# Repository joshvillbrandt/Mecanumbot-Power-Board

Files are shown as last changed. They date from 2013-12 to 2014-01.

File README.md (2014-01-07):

Mecanumbot Power Board
======================

The power board for the Mecanumbot robot.

## Features

* automatically selects between two batteries and the wall
* chooses the wall if available, otherwise drains the batteries one at a time
* provides power voltage and current measuring
* communicates to the primary vehicle Arduino over I2C
* provides regulated 5V power for the robot LEDs
* provides pins for an external switch

See more at http://javconcepts.com/2013/01/06/mecanumbot-power-board/.

## Todo List

* add battery charging
 * the [MAX164*](http://www.maximintegrated.com/datasheet/index.mvp/id/1751) can [allegedly](http://letsmakerobots.com/node/28374?page=1) charge up to a six cell lipo; i'm not sure if that includes balancing the cell or not too
* add fusing
* keep the board / robot powered during microcontroller restart by using flip-flops (useful for loading new code from the robot itself)
 * this could enable comm directly with ROS via USB instead of through I2C through the other Arduino!

## Screenshot

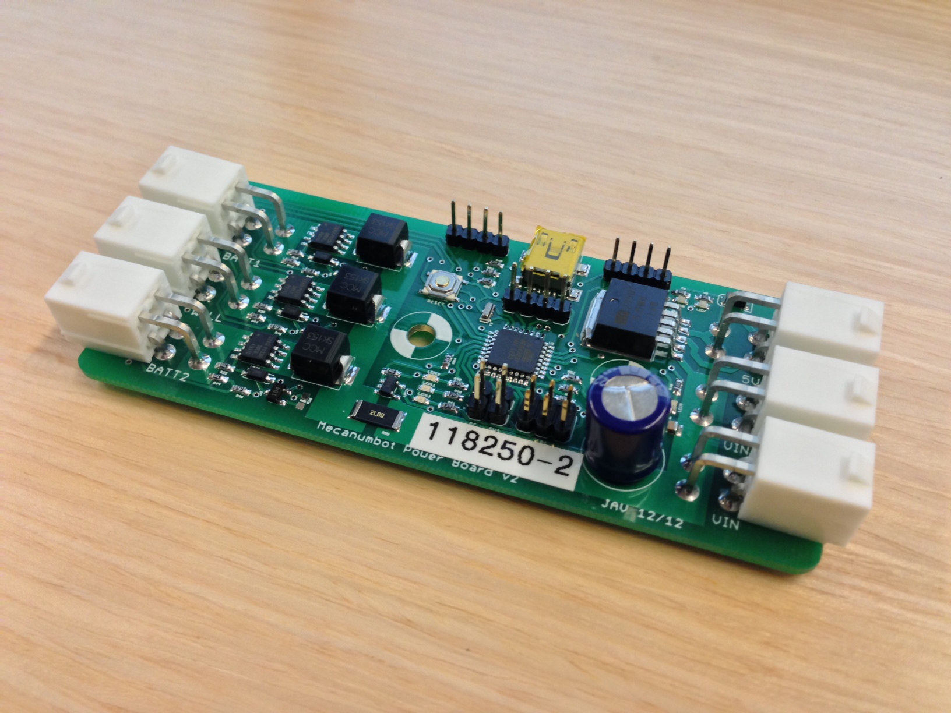
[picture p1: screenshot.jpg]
Assembled PCB Screenshot


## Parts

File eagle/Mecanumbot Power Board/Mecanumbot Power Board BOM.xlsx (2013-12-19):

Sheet: v1 BOM
Part | Value | Package | Description | Digi-Key PN | Cost
C2 | 1uF | 0603-CAP | Capacitor | 445-3452-1-ND | $0.03
C3 | 1uF | 0603-CAP | Capacitor | 445-3452-1-ND | $0.03
C4 | 0.1uF | 0603-CAP | Capacitor | 445-1316-1-ND | $0.01
C5 | 330uF | EIA3528 | footprint is wrong, but should work | P15095CT-ND | $0.92
C6 | 1uF | 0603-CAP | Capacitor | 445-3452-1-ND | $0.03
C7 | 0.1uF | 0603-CAP | Capacitor | 445-1316-1-ND | $0.01
C8 | 0.1uF | 0603-CAP | Capacitor | 445-1316-1-ND | $0.01
C10 | 0.1uF | 0603-CAP | Capacitor | 445-1316-1-ND | $0.01
C12 | 1uF | 0603-CAP | Capacitor | 445-3452-1-ND | $0.03
C13 | 1uF | 0603-CAP | Capacitor | 445-3452-1-ND | $0.03
C14 | 1uF | 0603-CAP | Capacitor | 445-3452-1-ND | $0.03
C15 | 0.1uF | 0603-CAP | Capacitor | 445-1316-1-ND | $0.01
C16 | 330uF | EIA3528 | footprint is wrong, but should work | P15095CT-ND | $0.92
C17 | 1uF | 0603-CAP | Capacitor | 445-3452-1-ND | $0.03
C18 | 68uF | EIA3216 | Capacitor Polarized | 493-6545-1-ND | $0.80
C19 | 220uF | CPOL-RADIAL-1000UF-25V | Capacitor Polarized | P5183-ND | $0.44
C21 | 0.1uF | 1206 | Capacitor | 399-1249-1-ND | $0.07
C22 | 0.1uF | 0603-CAP | Capacitor | 445-1316-1-ND | $0.01
C35 | 100uF | EIA3216 | Capacitor Polarized | 493-6545-1-ND | $0.80
J1 | AVR_SPI_PRG_6PTH | 2X3 | AVR ISP 6 Pin | 3M9459-ND | $0.42
JP1 | S2 | 1X02 | Header 2 | WM6436-ND | $0.90
JP6 | PWR LED | 1X02 | Header 2 | WM6436-ND | $0.90
JP7 | I2C | 1X04 | Header 4 | WM6436-ND | $0.90
LED1 | Red | LED-0603 | LEDs | 475-2512-1-ND | $0.08
LED2 | Yellow | LED-0603 | LEDs | 475-2558-1-ND | $0.08
LED3 | Green | LED-0603 | LEDs | 475-1409-1-ND | $0.07
LED4 | RED | LED5MM | LEDs | 1080-1120-ND | $0.33
LED5 | RED | LED5MM | LEDs | 1080-1120-ND | $0.33
LED6 | RED | LED5MM | LEDs | 1080-1120-ND | $0.33
Q1 |  | SOT23 | Transistor NPN | ZXTN07045EFFCT-ND | $0.59
Q2 |  | SOT23 | Transistor NPN | ZXTN07045EFFCT-ND | $0.59
Q3 |  | SOT23 | Transistor NPN | ZXTN07045EFFCT-ND | $0.59
R1 | 330 | 0603-RES | Resistor | 311-330GRCT-ND | $0.0048
R2 | 330 | 0603-RES | Resistor | 311-330GRCT-ND | $0.0048
R3 | 10K | 0603-RES | Resistor | 311-10KGRCT-ND | $0.0048
R4 | 7.5K | 0603-RES | Resistor | 311-7.5KGRCT-ND | $0.01
R5 | 7.5K | 0603-RES | Resistor | 311-7.5KGRCT-ND | $0.01
R6 | 200K | 0603-RES | Resistor | 311-200KGRCT-ND | $0.01
R7 | 24K | 0603-RES | Resistor | 311-24KGRCT-ND | $0.01
R8 | 1K | 0603-RES | Resistor | 311-1.0KGRCT-ND | $0.01
R9 | 200K | 0603-RES | Resistor | 311-200KGRCT-ND | $0.01
R10 | 24K | 0603-RES | Resistor | 311-24KGRCT-ND | $0.01
R11 | 1K | 0603-RES | Resistor | 311-1.0KGRCT-ND | $0.01
R12 | 10K | 0603-RES | Resistor | 311-10KGRCT-ND | $0.0048
R13 | 10K | 0603-RES | Resistor | 311-10KGRCT-ND | $0.0048
R14 | 10K | 0603-RES | Resistor | 311-10KGRCT-ND | $0.0048
R15 | 10K | 0603-RES | Resistor | 311-10KGRCT-ND | $0.0048
R16 | 10K | 0603-RES | Resistor | 311-10KGRCT-ND | $0.0048
R17 | 10K | 0603-RES | Resistor | 311-10KGRCT-ND | $0.0048
R18 | 330 | 0603-RES | Resistor | 311-330GRCT-ND | $0.0048
R19 | 330 | 0603-RES | Resistor | 311-330GRCT-ND | $0.0048
R20 | 330 | 0603-RES | Resistor | 311-330GRCT-ND | $0.0048
R21 | 330 | 0603-RES | Resistor | 311-330GRCT-ND | $0.0048
R22 | 10K | 0603-RES | Resistor | 311-10KGRCT-ND | $0.0048
R23 | 10K | 0603-RES | Resistor | 311-10KGRCT-ND | $0.0048
R24 | 10K | 0603-RES | Resistor | 311-10KGRCT-ND | $0.0048
R25 | 10K | 0603-RES | Resistor | 311-10KGRCT-ND | $0.0048
R26 | 3.3K | 0603-RES | Resistor | 311-3.3KGRCT-ND | $0.0048
R27 | 3.3K | 0603-RES | Resistor | 311-3.3KGRCT-ND | $0.0048
R28 | 3.3K | 0603-RES | Resistor | 311-3.3KGRCT-ND | $0.0048
R29 | 3.3K | 0603-RES | Resistor | 311-3.3KGRCT-ND | $0.0048
R30 | 330 | 0603-RES | Resistor | 311-330GRCT-ND | $0.0048
R31 | 82.5K 1% | 0603-RES | Resistor | 311-82.5KHRCT-ND | $0.01
R32 | 0.002 1% 2W | R2512 | Resistor | RHM.002AUCT-ND | $0.85
R33 | 3.3K | 0603-RES | Resistor | 311-3.3KGRCT-ND | $0.0048
R34 | 10K | 0603-RES | Resistor | 311-10KGRCT-ND | $0.0048
R35 | 10k | 0603-RES | Resistor | 311-10KGRCT-ND | $0.0048
R36 | 10k | 0603-RES | Resistor | 311-10KGRCT-ND | $0.0048
R37 | 10k | 0603-RES | Resistor | 311-10KGRCT-ND | $0.0048
S1 | reset | TACTILE_SWITCH_SMD |  | CKN9104CT-ND | $0.61
U$1 | IR3477 | IR3477 |  | IR3477MTR1PBFCT-ND | $6.35
U$2 | 1uH | CDRH125 | Inductors | 308-1334-1-ND | $1.35
U$3 | IR3477 | IR3477 |  | IR3477MTR1PBFCT-ND | $6.35
U$4 | 1uH | CDRH125 | Inductors | 308-1334-1-ND | $1.35
U$5 | DIODE_SCHOTTKY | DO214AB |  | SK153-TPCT-ND | $1.19
U$6 | MOSFET-PCHANNEL-SOIC8SOIC8 | SO08 |  | IRF9310TRPBFCT-ND | $1.36
U$7 | MOSFET-PCHANNEL-SOIC8SOIC8 | SO08 |  | IRF9310TRPBFCT-ND | $1.36
U$8 | DIODE_SCHOTTKY | DO214AB |  | SK153-TPCT-ND | $1.19
U$9 | TERMINAL-4MINIFIT-JR | MINIFITJR-RGT-4 |  | WM21352-ND | $0.84
U$10 | MOSFET-PCHANNEL-SOIC8SOIC8 | SO08 |  | IRF9310TRPBFCT-ND | $1.36
U$11 | DIODE_SCHOTTKY | DO214AB |  | SK153-TPCT-ND | $1.19
U$12 | TERMINAL-4MINIFIT-JR | MINIFITJR-RGT-4 |  | WM21352-ND | $0.84
U$13 | TERMINAL-4MINIFIT-JR | MINIFITJR-RGT-4 |  | WM21352-ND | $0.84
U$14 | TERMINAL-4MINIFIT-JR | MINIFITJR-RGT-4 |  | WM21352-ND | $0.84
U$15 | TERMINAL-4MINIFIT-JR | MINIFITJR-RGT-4 |  | WM21352-ND | $0.84
U$16 | TERMINAL-4MINIFIT-JR | MINIFITJR-RGT-4 |  | WM21352-ND | $0.84
U$17 | TERMINAL-4MINIFIT-JR | MINIFITJR-RGT-4 |  | WM21352-ND | $0.84
U$18 | TERMINAL-4MINIFIT-JR | MINIFITJR-RGT-4 |  | WM21352-ND | $0.84
U$19 | VREG-MIC29501-5V | TO263-5 |  | 576-2240-ND | $5.60
U$20 | INA139/169SOT23-5 | SOT23-5 | TI High-Side Measurement: CURRENT SHUNT MONITOR | INA139NA/250CT-ND | $2.15
U$21 | SUPERCAPS-LEAD | AVX-SUPERCAP-S-LEAD | CAP SUPER 6.8MF 15V BZ05 SMD | 478-6277-ND | $16.36
U$22 | HMC6352 | LCC24 | HMC6352 | 342-1041-1-ND | $26.00
U1 | FT232RL-BASICSSOP | SSOP28DB | USB UART | 768-1007-1-ND | $4.50
U2 | ATMEGA168 | TQFP32-08 |  | ATMEGA328P-AU-ND | $3.05
X1 | USBSMD | USB-MINIB | USB Connectors | ED2992CT-ND | $0.68
Y1 | RESONATORSMD | RESONATOR-SMD | Resonator | 490-1198-1-ND | $0.95
Total |  |  |  |  | $101.10
 | fuse holder | http://www.digikey.com/product-detail/en/01530008Z/F065-ND/183334
 | fuse | http://www.digikey.com/product-detail/en/0297015.WXNV/F992-ND/146594
 |  | http://www.digikey.com/product-detail/en/MB2181SS1W01-CA/360-2178-ND/1014874

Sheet: v2 BOM
Qty | Parts | Digi-Key PN | Value | Device | Package | Description | Cost | Sub-total
12 | R3, R6, R12, R13, R14, R15, R16, R17, R23, R24, R25, R34, R37 | 311-10.0KHRCT-ND | 10K | RESISTOR0603-RES | 0603-RES | Resistor | $0.10 | $1.20
8 | R1, R2, R4, R18, R19, R20, R21, R30 | 311-330GRCT-ND | 330 | RESISTOR0603-RES | 0603-RES | Resistor | $0.0048 | $0.04
6 | U$12, U$13, U$14, U$16, U$17, U$18 | WM21352-ND | TERMINAL-4MINIFIT-JR | TERMINAL-4MINIFIT-JR | MINIFITJR-RGT-4 |  | $0.84 | $5.04
5 | R7, R27, R28, R29, R33 | 311-3.30KHRCT-ND | 3.3K | RESISTOR0603-RES | 0603-RES | Resistor | $0.10 | $0.50
3 | Q1, Q2, Q3 | ZXTN07045EFFCT-ND |  | TRANSISTOR_NPNSOT23 | SOT23 | Transistor NPN | $0.59 | $1.77
3 | C7, C8, C10 | 445-1316-1-ND | .1uF | CAP0603-CAP | 0603-CAP | Capacitor | $0.01 | $0.03
3 | U$2, U$3, U$4 | BZT52C33-FDICT-ND | BZT52C33-FDICT-ND | BZT52C33-FDICT-ND | SOD-123 | 33V Zener Diode, 500mW | $0.21 | $0.63
3 | U$5, U$8, U$11 | SK153-TPCT-ND | DIODE_SCHOTTKY | DIODE_SCHOTTKY | DO214AB |  | $1.19 | $3.57
3 | U$6, U$7, U$10 | IRF9310TRPBFCT-ND | MOSFET-PCHANNEL-SOIC8SOIC8 | MOSFET-PCHANNEL-SOIC8SOIC8 | SO08 |  | $1.36 | $4.08
3 | LED4, LED5, LED6 | 475-2816-1-ND | Blue | LED0603 | LED-0603 | LEDs | $0.17 | $0.52
2 | JP1, PC-CTRL | WM6436-ND | S2 | M02PTH | 1X02 | Header 2 | $0.90 | $1.80
2 | LED2, LED3 | 475-2558-1-ND | Yellow | LED0603 | LED-0603 | LEDs | $0.08 | $0.16
1 | R32 | RHM.002AUCT-ND | 0.002 1% 2W | RESISTOR2512 | R2512 | Resistor | $0.85 | $0.85
1 | C21 | 399-1249-1-ND | 0.1uF | CAP1206 | 1206 | Capacitor | $0.07 | $0.07
1 | C35 | 493-6545-1-ND | 100uF | CAP_POL1206 | EIA3216 | Capacitor Polarized | $0.80 | $0.80
1 | C19 | P5183-ND | 220uF | CAP_POLPTH4 | CPOL-RADIAL-1000UF-25V | Capacitor Polarized | $0.44 | $0.44
1 | R31 | 311-82.5KHRCT-ND | 82.5K 1% | RESISTOR0603-RES | 0603-RES | Resistor | $0.01 | $0.01
1 | U2 | ATMEGA328P-AU-ND | ATMEGA168 | ATMEGA168 | TQFP32-08 |  | $3.05 | $3.05
1 | J1 | 3M9459-ND | AVR_SPI_PRG_6PTH | AVR_SPI_PRG_6PTH | 2X3 | AVR ISP 6 Pin | $0.42 | $0.42
1 | U$1 | CLA230TR-ND | CLA230TR-NDSMD | CLA230TR-NDSMD | 4-SOP | Digi-Key part: CLA230TR-ND | $0.63 | $0.63
1 | U1 | 768-1007-1-ND | FT232RL-BASICSSOP | FT232RL-BASICSSOP | SSOP28DB | USB UART | $4.50 | $4.50
1 | LED1 | 475-2512-1-ND | RED | LED0603 | LED-0603 | LEDs | $0.08 | $0.08
1 | JP2, JP3, JP7 | WM6436-ND | USB, PWR-CTRL, I2C | M04PTH | 1X04 | Header 4 | $0.90 | $0.90
1 | U$20 | INA139NA/250CT-ND | INA139/169SOT23-5 | INA139/169SOT23-5 | SOT23-5 | TI High-Side Measurement: CURRENT SHUNT MONITOR | $2.15 | $2.15
1 | Y1 | 490-1198-1-ND | RESONATORSMD | RESONATORSMD | RESONATOR-SMD | Resonator | $0.95 | $0.95
1 | X1 | ED2992CT-ND | USBSMD | USBSMD | USB-MINIB | USB Connectors | $0.68 | $0.68
1 | U$19 | 576-2240-ND | VREG-MIC29501-5V | VREG-MIC29501-5V | TO263-5 |  | $5.60 | $5.60
1 | S1 | CKN9104CT-ND | reset | SWITCH-MOMENTARY-2SMD | TACTILE_SWITCH_SMD |  | $0.61 | $0.61
Total |  |  |  |  |  |  |  | $41.08

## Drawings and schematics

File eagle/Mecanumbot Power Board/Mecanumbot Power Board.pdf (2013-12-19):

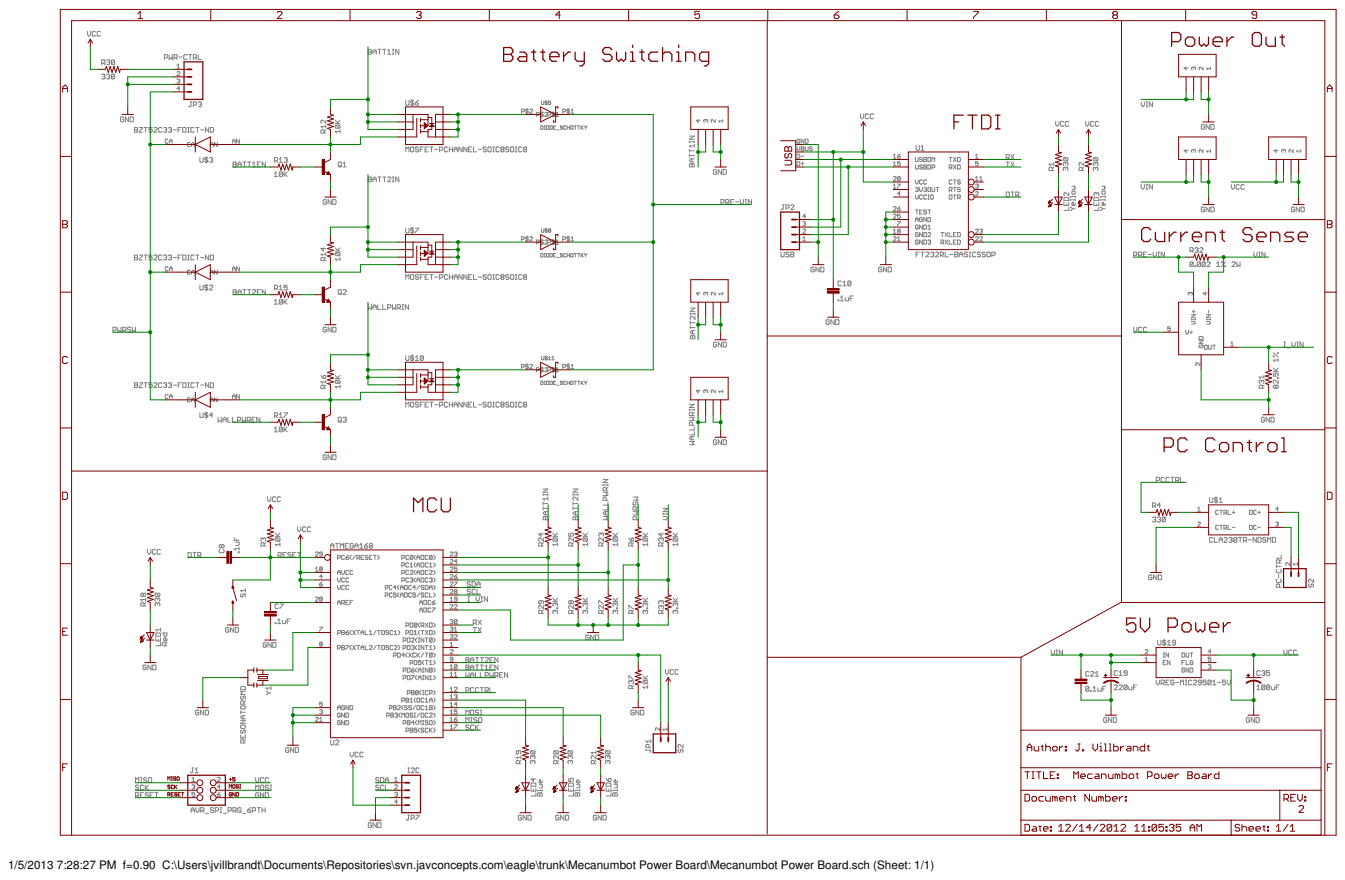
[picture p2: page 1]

1/5/2013 7:28:27 PM f=0.90 C:\Users\jvillbrandt\Documents\Repositories\svn.javconcepts.com\eagle\trunk\Mecanumbot Power Board\Mecanumbot Power Board.sch (Sheet: 1/1)

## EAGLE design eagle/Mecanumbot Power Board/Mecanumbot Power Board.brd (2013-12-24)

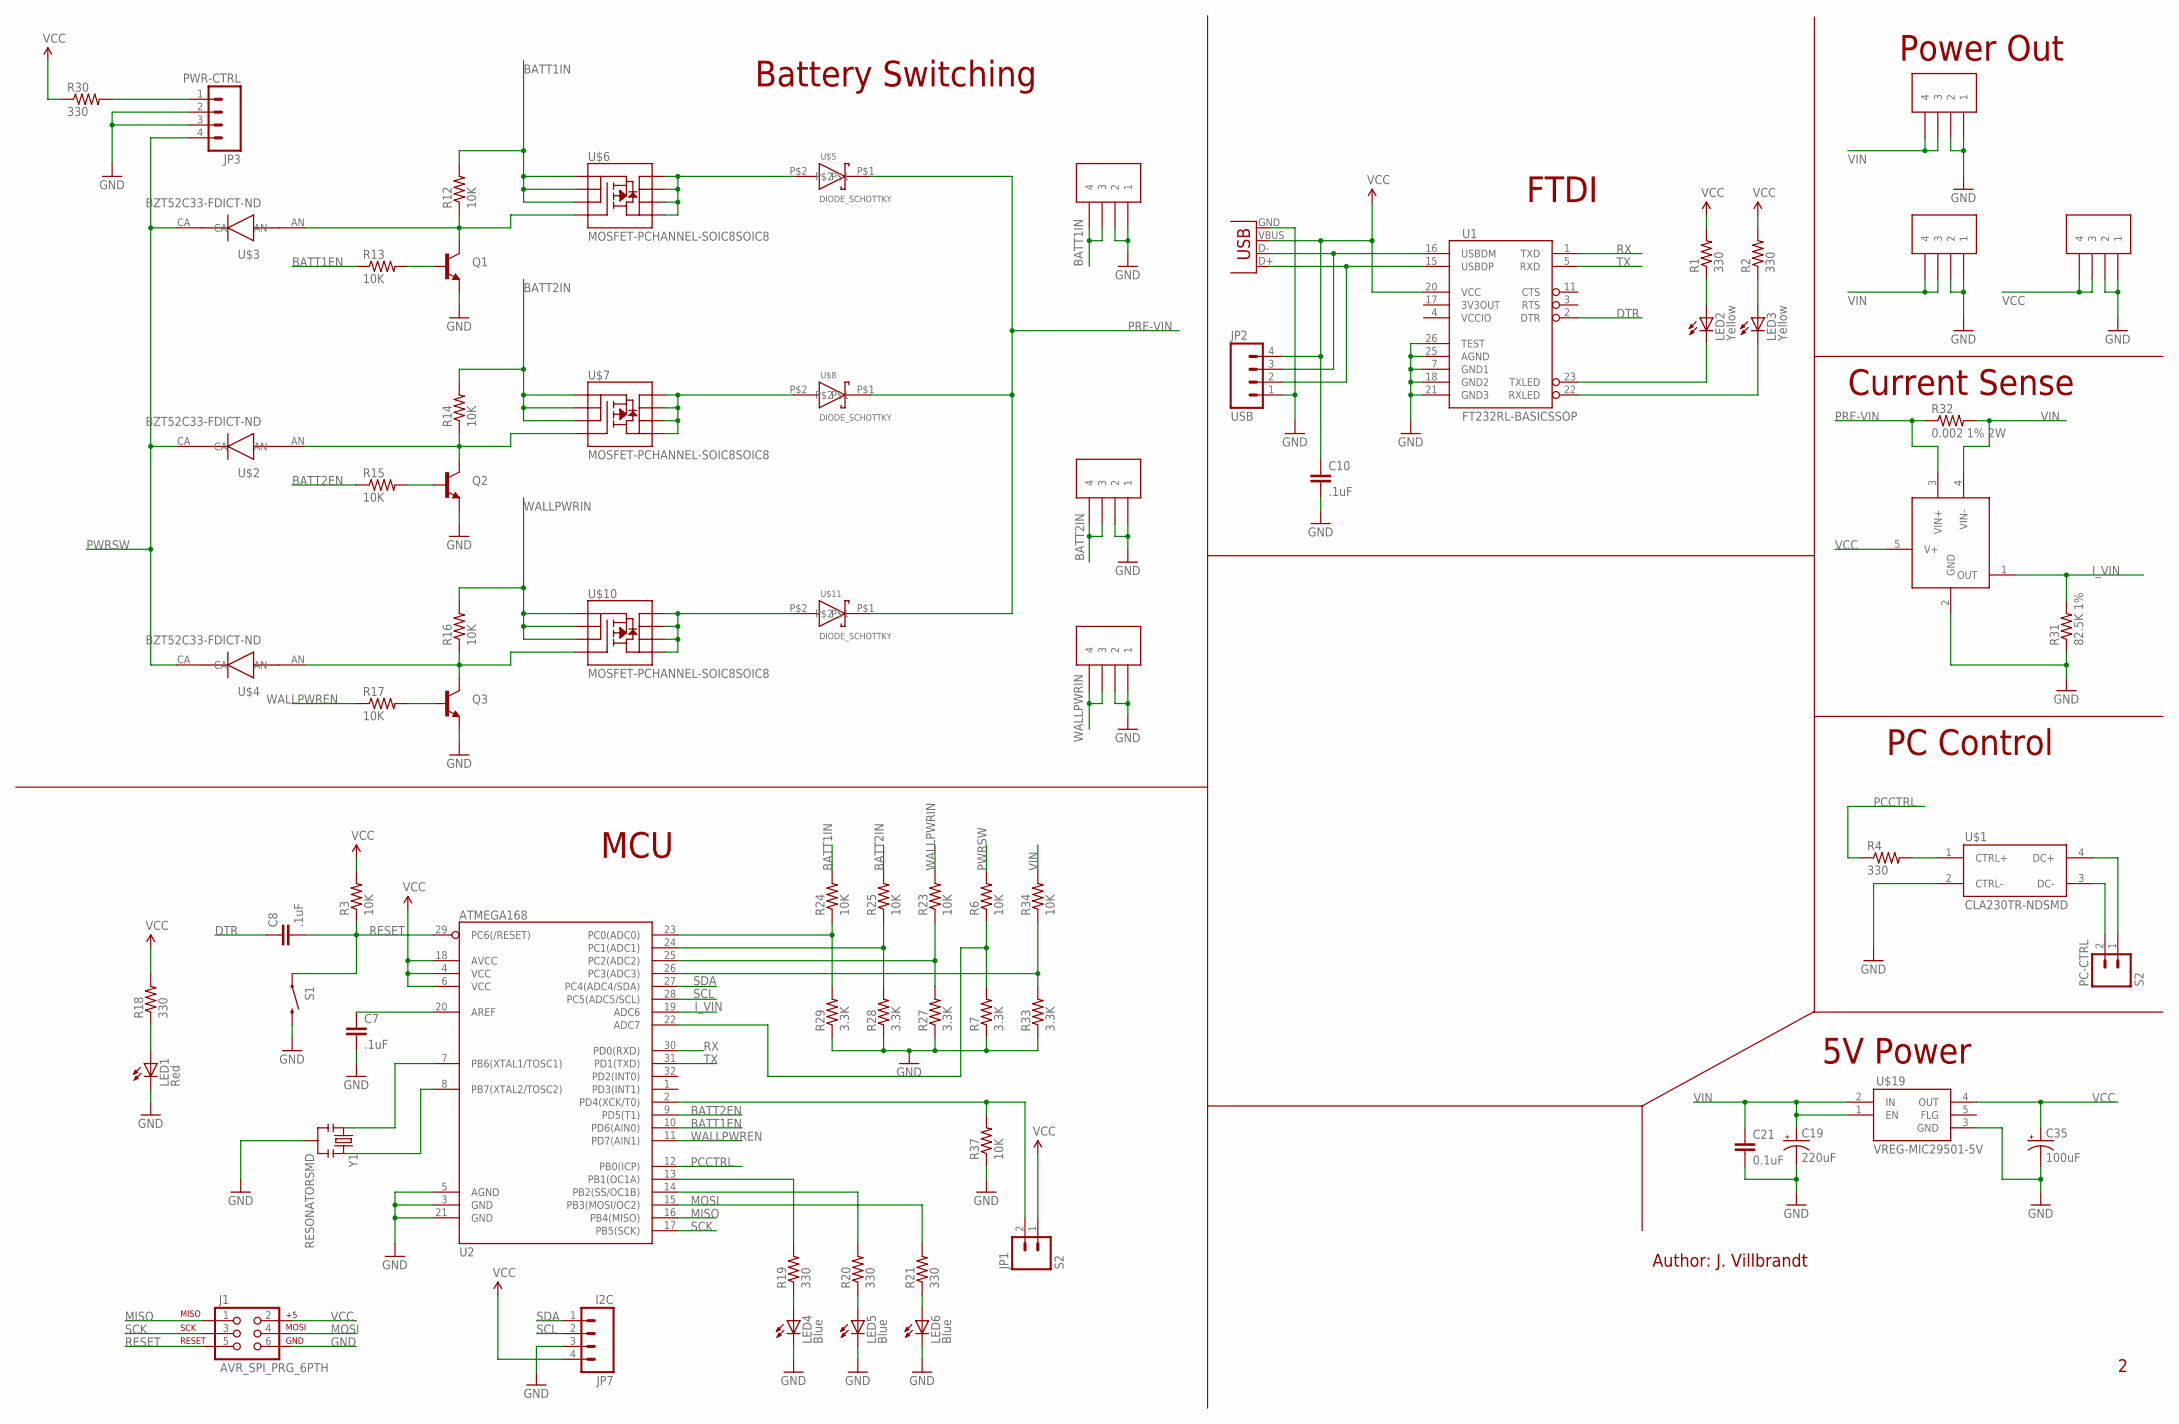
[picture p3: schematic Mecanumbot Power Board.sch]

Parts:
C7, C8, C10: .1uF; 0603-CAP
C19: 220uF; CPOL-RADIAL-1000UF-25V
C21: 0.1uF; 1206
C35: 100uF; EIA3216
J1: AVR_SPI_PRG_6PTH; 2X3
JP1: S2; 1X02
JP2: USB; 1X04
JP3: PWR-CTRL; 1X04
JP7: I2C; 1X04
LED1: Red; LED-0603
LED2, LED3: Yellow; LED-0603
LED4, LED5, LED6: Blue; LED-0603
PC-CTRL: S2; 1X02
Q1, Q2, Q3: TRANSISTOR_NPNSOT23; SOT23
R1, R2, R4, R18, R19, R20, R21, R30: 330; 0603-RES
R3, R6, R12, R13, R14, R15, R16, R17, R23, R24, R25, R34, R37: 10K; 0603-RES
R7, R27, R28, R29, R33: 3.3K; 0603-RES
R31: 82.5K 1%; 0603-RES
R32: 0.002 1% 2W; R2512
S1: reset; TACTILE_SWITCH_SMD
U1: FT232RL-BASICSSOP; SSOP28DB
U2: ATMEGA168; TQFP32-08
U$1: CLA230TR-NDSMD; 4-SOP
U$2, U$3, U$4: BZT52C33-FDICT-ND; SOD-123
U$5, U$8, U$11: DIODE_SCHOTTKY; DO214AB
U$6, U$7, U$10: MOSFET-PCHANNEL-SOIC8SOIC8; SO08
U$12, U$13, U$14, U$16, U$17, U$18: TERMINAL-4MINIFIT-JR; MINIFITJR-RGT-4
U$19: VREG-MIC29501-5V; TO263-5
U$20: INA139/169SOT23-5; SOT23-5
X1: USBSMD; USB-MINIB
Y1: RESONATORSMD; RESONATOR-SMD

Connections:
BATT1EN: R13.1, U2.10 (PD6(AIN0))
BATT1IN: R12.2, R24.2, U$6.1 (S), U$6.2 (S), U$6.3 (S), U$12.3, U$12.4
BATT1PREDIODE: U$5.P$2, U$6.5 (D), U$6.6 (D), U$6.7 (D), U$6.8 (D)
BATT2EN: R15.1, U2.9 (PD5(T1))
BATT2IN: R14.2, R25.2, U$7.1 (S), U$7.2 (S), U$7.3 (S), U$13.3, U$13.4
BATT2PREDIODE: U$7.5 (D), U$7.6 (D), U$7.7 (D), U$7.8 (D), U$8.P$2
DTR: C8.1, U1.2 (DTR)
GND: C7.2, C10.2, C19.2 (-), C21.2, C35.C (-), J1.6, JP2.1, JP3.2, JP3.3, JP7.3, LED1.C, LED4.C, LED5.C, LED6.C, Q1.2 (E), Q2.2 (E), Q3.2 (E), R7.1, R27.1, R28.1, R29.1, R31.1, R33.1, R37.1, S1.3 (2), U1.7 (GND1), U1.18 (GND2), U1.21 (GND3), U1.25 (AGND), U1.26 (TEST), U2.3 (GND), U2.5 (AGND), U2.21 (GND), U$1.2 (CTRL-), U$12.1, U$12.2, U$13.1, U$13.2, U$14.1, U$14.2, U$16.1, U$16.2, U$17.1, U$17.2, U$18.1, U$18.2, U$19.3 (GND), U$20.2 (GND), X1.GND, Y1.2
I_VIN: R31.2, U2.19 (ADC6), U$20.1 (OUT)
MISO: J1.1, U2.16 (PB4(MISO))
MOSI: J1.4, R21.2, U2.15 (PB3(MOSI/OC2))
unnamed: LED2.A, R1.1
unnamed: LED3.A, R2.1
unnamed: LED2.C, U1.23 (TXLED)
unnamed: LED3.C, U1.22 (RXLED)
unnamed: PC-CTRL.2, U$1.3 (DC-)
unnamed: PC-CTRL.1, U$1.4 (DC+)
unnamed: JP2.3, U1.16 (USBDM), X1.D-
unnamed: JP2.2, U1.15 (USBDP), X1.D+
unnamed: C7.1, U2.20 (AREF)
unnamed: U2.7 (PB6(XTAL1/TOSC1)), Y1.1
unnamed: U2.8 (PB7(XTAL2/TOSC2)), Y1.3
unnamed: R4.2, U$1.1 (CTRL+)
unnamed: JP3.1, R30.2
unnamed: R20.2, U2.14 (PB2(SS/OC1B))
unnamed: R33.2, R34.1, U2.26 (PC3(ADC3))
unnamed: R19.2, U2.13 (PB1(OC1A))
unnamed: JP1.2, R37.2, U2.2 (PD4(XCK/T0))
unnamed: Q1.3 (C), R12.1, U$3.AN, U$6.4 (G)
unnamed: Q1.1 (B), R13.2
unnamed: Q2.3 (C), R14.1, U$2.AN, U$7.4 (G)
unnamed: Q2.1 (B), R15.2
unnamed: LED1.A, R18.1
unnamed: Q3.3 (C), R16.1, U$4.AN, U$10.4 (G)
unnamed: Q3.1 (B), R17.2
unnamed: LED6.A, R21.1
unnamed: LED4.A, R19.1
unnamed: LED5.A, R20.1
unnamed: R23.1, R27.2, U2.25 (PC2(ADC2))
unnamed: R25.1, R28.2, U2.24 (PC1(ADC1))
unnamed: R24.1, R29.2, U2.23 (PC0(ADC0))
unnamed: R6.1, R7.2, U2.22 (ADC7)
PCCTRL: R4.1, U2.12 (PB0(ICP))
PRE-VIN: R32.1, U$5.P$1, U$8.P$1, U$11.P$1, U$20.3 (VIN+)
PWRSW: JP3.4, R6.2, U$2.CA, U$3.CA, U$4.CA
RESET: C8.2, J1.5, R3.1, S1.1, U2.29 (PC6(/RESET))
RX: U1.1 (TXD), U2.30 (PD0(RXD))
SCK: J1.3, U2.17 (PB5(SCK))
SCL: JP7.2, U2.28 (PC5(ADC5/SCL))
SDA: JP7.1, U2.27 (PC4(ADC4/SDA))
TX: U1.5 (RXD), U2.31 (PD1(TXD))
VCC: C10.1, C35.A (+), J1.2, JP1.1, JP2.4, JP7.4, R1.2, R2.2, R3.2, R18.2, R30.1, U1.20 (VCC), U2.4 (VCC), U2.6 (VCC), U2.18 (AVCC), U$18.3, U$18.4, U$19.4 (OUT), U$20.5 (V+), X1.VBUS
VCCIO: U1.4 (VCCIO)
VIN: C19.1 (+), C21.1, R32.2, R34.2, U$16.3, U$16.4, U$17.3, U$17.4, U$19.1 (EN), U$19.2 (IN), U$20.4 (VIN-)
WALLPWREN: R17.1, U2.11 (PD7(AIN1))
WALLPWRIN: R16.2, R23.2, U$10.1 (S), U$10.2 (S), U$10.3 (S), U$14.3, U$14.4
WALLPWRPREDIODE: U$10.5 (D), U$10.6 (D), U$10.7 (D), U$10.8 (D), U$11.P$2

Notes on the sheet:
Battery Switching
MCU
FTDI
5V Power
Power Out
Current Sense
Author: J. Villbrandt
PC Control

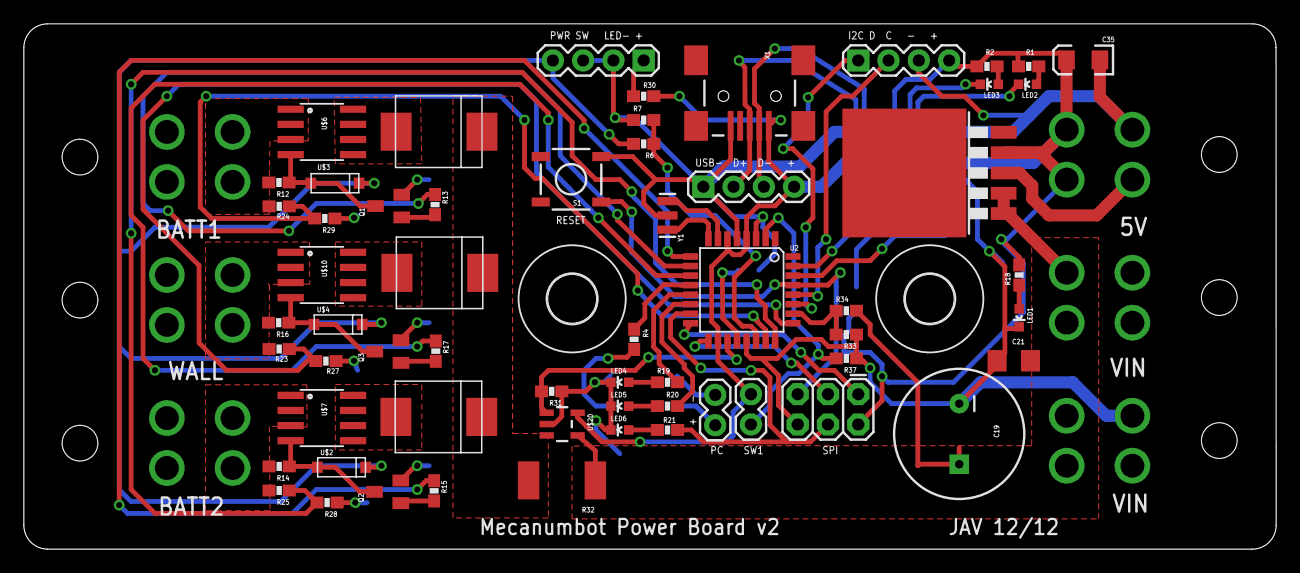
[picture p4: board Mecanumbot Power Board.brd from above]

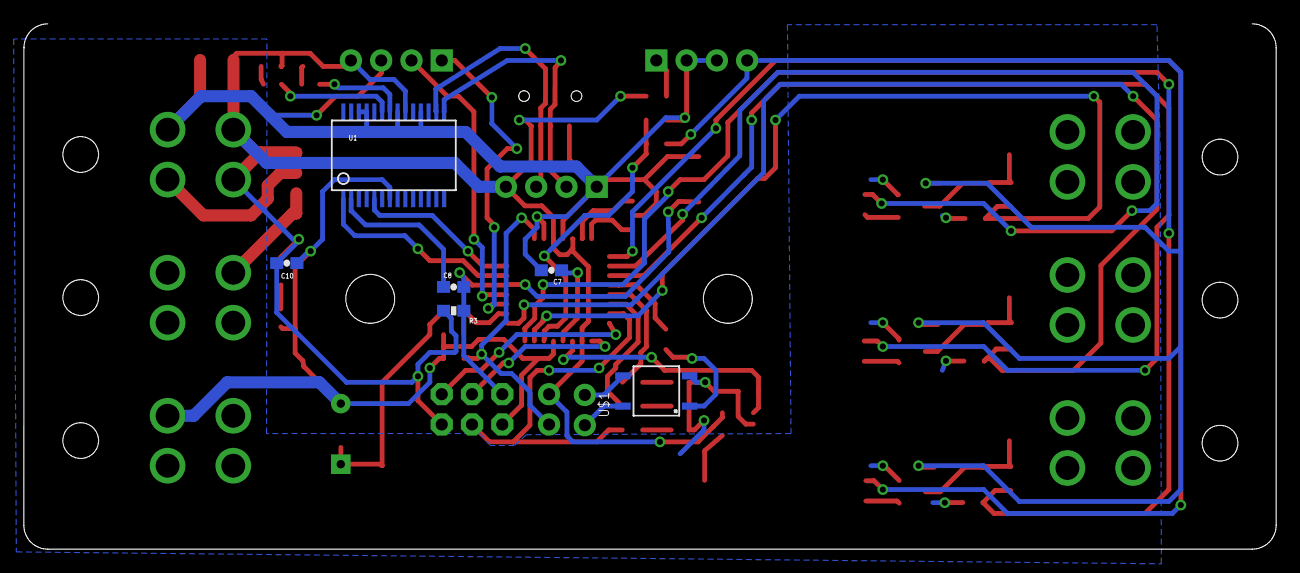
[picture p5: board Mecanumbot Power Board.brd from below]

Board: 2 copper layers, 105.1 x 44.1 mm, 74 parts (6 on the bottom side), 56 nets.

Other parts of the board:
U$24, U$26: 4,1

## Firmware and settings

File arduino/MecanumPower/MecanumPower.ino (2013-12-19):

/*
  MecanumPower.ino - Controls power input for the Mecanumbot.
  Created by Josh Villbrandt (http://javconcepts.com/), 10/12-1/13.
  Released into the public domain.
*/

// Set up I2C
//#include <Wire.h>

#define DEBUG false
#define PC_STARTUP true
#define REF_5V 4.973 // V
#define ADC_COUNTS 1023.0 // counts
#define ADC_V_MULT ((REF_5V / ADC_COUNTS) / 0.24) // counts to V
#define ADC_I_MULT ((REF_5V / ADC_COUNTS) * (1000.0 / (0.002 * 82500))) // counts to A
#define MIN_VOLT 10.5 // V
#define TURN_OFF_DEBOUNCE 1500 // ms
#define LED_RATE 100 // ms
#define LED_DUTY 65 // ms

// Define I/O pins
#define EXT_SW 4
#define EXT_PC 8
byte ledPins[] = {10, 9, 11}; //wall, batt1, batt2
byte fetPins[] = {7, 6, 5}; //wall, batt1, batt2
byte voltagePins[] = {A2, A0, A1, A3, A7}; //wall, batt1, batt2, VIN, PWRSW
byte currentPins[] = {A6};

// State variables
float voltageReadings[] = {0.0, 0.0, 0.0, 0.0, 0.0};
float currentReadings[] = {0.0};
boolean availableSource[] = {true, false, false};
boolean activeSource[] = {true, false, false};
long loopStart = 0;
long loopEnd = 0;
boolean startup = true;
boolean pwrswState = false;
boolean lastPwrswState = false;
long pwrswDebounceTime = 0;
boolean stayPowered = true;

void setup() {
  if(DEBUG) Serial.begin(57600);
  
  // set external interface pins
  pinMode(EXT_SW, INPUT);
  pinMode(EXT_PC, OUTPUT);
  
  // set fet outputs
  for(int i = 0 ; i < 3; i++) {
    pinMode(fetPins[i], OUTPUT);
  }
}

void loop() {
  if(DEBUG) loopStart = micros();
  
  // voltage inputs
  for(int i = 0; i < 5; i++) {
    int sensorValue = analogRead(voltagePins[i]);
    voltageReadings[i] = sensorValue * ADC_V_MULT;
    
    // power source calcs
    if(i <= 2) {
      availableSource[i] = (voltageReadings[i] >= MIN_VOLT);
    }
  }
  
  // current inputs
  for(int i = 0; i < 1; i++) {
    int sensorValue = analogRead(currentPins[i]);
    currentReadings[i] = sensorValue * ADC_I_MULT;
  }
  
  // choose active source
  for(int i = 0 ; i < 3; i++) activeSource[i] = false;
  if(availableSource[0]) activeSource[0] = true; // prefer the wall outlet
  else {
    int voltageMin = 99;
    int indexMin = -1;
    for(int i = 1 ; i < 3; i++) {
      if(availableSource[i] && voltageReadings[i] < voltageMin) {
        voltageMin = voltageReadings[i];
        indexMin = i;
      }
    }
    if(indexMin >= 0) activeSource[indexMin] = true;
    else stayPowered = false; // forcing a clean shutdown, otherwise the uC jitters
  }
  // TODO: this should really have a persistance value and not change source right away (when multiple are present)
  
  // set active source
  for(int i = 0 ; i < 3; i++) {
    // control MOSFET
    if(activeSource[i] && (stayPowered || pwrswState)) digitalWrite(fetPins[i], HIGH);
    else digitalWrite(fetPins[i], LOW);
    
    // set LED
    if(activeSource[i] && (stayPowered || pwrswState)) {
      // fancy active indication
      if(millis() % LED_RATE < LED_DUTY) analogWrite(ledPins[i], 255);
      else analogWrite(ledPins[i], 0);
    }
    else if(availableSource[i]) analogWrite(ledPins[i], 127);
    else analogWrite(ledPins[i], 1);
  }
  
  // external PC control
  if(startup && millis() > 3000 && millis() < 4000) digitalWrite(EXT_PC, HIGH);
  else digitalWrite(EXT_PC, LOW);
  if(millis() > 4000) startup = false;
  
  // turn off board
  pwrswState = (!startup && voltageReadings[4] < 5.0); // voltageReadings[4] is not calibrated correctly
  if(pwrswState != lastPwrswState) pwrswDebounceTime = millis();
  if(pwrswState && (millis() - pwrswDebounceTime) > TURN_OFF_DEBOUNCE) stayPowered = false;
  lastPwrswState = pwrswState;
  
  // TODO: send I2C message to master if asked for
  
  // Debug
  if(DEBUG) {
    loopEnd = micros() - loopStart;
    
    Serial.println("MecanumPower Debug");
    
    Serial.print("e_batt1: \t");
    Serial.print(voltageReadings[1]);
    Serial.println(" V");
    
    Serial.print("e_wall:  \t");
    Serial.print(voltageReadings[0]);
    Serial.println(" V");
    
    Serial.print("e_batt2: \t");
    Serial.print(voltageReadings[2]);
    Serial.println(" V");
    
    Serial.print("e_vin:   \t");
    Serial.print(voltageReadings[3]);
    Serial.println(" V");
    
    Serial.print("i_vin:   \t");
    Serial.print(currentReadings[0]);
    Serial.println(" A");
    
    Serial.print("pwr_sw:  \t");
    Serial.println(pwrswState);
    
    Serial.print("ext_sw:  \t");
    Serial.println(digitalRead(EXT_SW));
    
    Serial.print("loop tm: \t");
    Serial.print(loopEnd);
    Serial.println(" us");
    
    delay(500);
    Serial.println();
  }
}

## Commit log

2013-12-19 initial commit from svn
    [IR3477 Calculator.xlsx, Mecanumbot Power Board BOM.xlsx, Mecanumbot Power Board.brd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]
2013-12-24 pushing rev 1.0 from svn
    [IR3477 Calculator.xlsx]
2013-12-24 pushing back version 1.0 from svn
    [IR3477 Calculator.xlsx, Mecanumbot Power Board BOM.xlsx, Mecanumbot Power Board.brd]
2013-12-24 pushing back v2.0 from svn
    [Mecanumbot Power Board BOM.xlsx, Mecanumbot Power Board.brd, Mecanumbot Power Board.sch]
2014-01-07 added battery charging circuit links
